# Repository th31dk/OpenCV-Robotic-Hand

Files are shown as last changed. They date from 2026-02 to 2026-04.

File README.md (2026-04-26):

<h1 align="center">
    EchoHand
</h1>
<h4 align="center">
    A robot hand that mirror's your every gesture
</h4>



<h2 align="center">
A Bit About This Project
</h2>
This project originally started as a ASL Interpreter. However, while researching ways to teach it signs, I discovered computer vision and how you can make robots copy you. Last year, I went to Prototype, a hackathon hosted by Hack Club. There, we had to train these SO-101 Robotic Arms to perform certain actions. The teleoperator part of the training stuck to me the most, so this project was born!

<h2 align="center">
Assembly
</h2>

### Hardware
#### [Bill Of Materials](/BOM)
|Part Number|Part Name |Quantity|Sourcing Link |Cost  |Notes|
|---|---|---|---|---|-----|
|1 |Arduino Uno |1 |https://www.aliexpress.us/item/3256808569187520.html|$5.65 | |
|2 |Breadboard |1 |https://www.aliexpress.us/item/3256806927240551.html|$1.92 | |
|3 |Dupont Wires |17 |https://a.co/d/0hN85zCM |$8.99 | |
|4 |External Power Supply|1 |https://a.co/d/045DWk0g |$59.99| |
|5 |DS3225 Servo |5 |https://a.co/d/0iK4KOZB |$90.00| |
|6 |M3x10mm BHCS |24 |https://www.aliexpress.us/item/2255800794906149.html|$1.86 | |
|7 |M3x10mm SHCS |2 |https://www.aliexpress.us/item/3256804341271555.html|$1.50 | |
|8 |USB-A to USB-B Cable |1 |https://a.co/d/0aNsTbvj |$7.21 | |
|9 |Webcam |1 |https://a.co/d/0bebSZXz |$25.00| |
|10 |Fishing Line |2000mm  |https://a.co/d/07G4QxGr |$9.98 | |
|11 |Elastic Cord |600mm |https://a.co/d/07XXOlZX |$9.99 | |

### [3D Printed Parts](/List%20Of%203D%20Printed%20Parts.csv)
3D files can be found [here](/Print%20Files/)

|Part Number|Part Name |Quantity|Material |Total Grams|Notes |
|---|---|---|---|---|---|
|1 |Finger 1 |5 |PLA |17.69 | |
| | | |PETG |0.34 |PETG for easy support removal|
|2 |Finger 2 |5 |PLA |20.15 | |
| | | |PETG |0.38 |PETG for easy support removal|
|3 |Finger 3 |4 |PLA |14.95 | |
| | | |PETG |0.37 |PETG for easy support removal|
|4 |Thumb |1 |PLA |7.33 | |
| | | |PETG |0.77 |PETG for easy support removal|
|5 |BackStand |1 |PLA |133.6 | |
|6 |Palm |1 |PLA |28.9 | |
|7 |Pin |11 |PLA |0.71 | |
|8 |Spool |10 |PLA |23.44 | |
|9 |Support |1 |PLA |44.39 | |

### Wiring Diagram
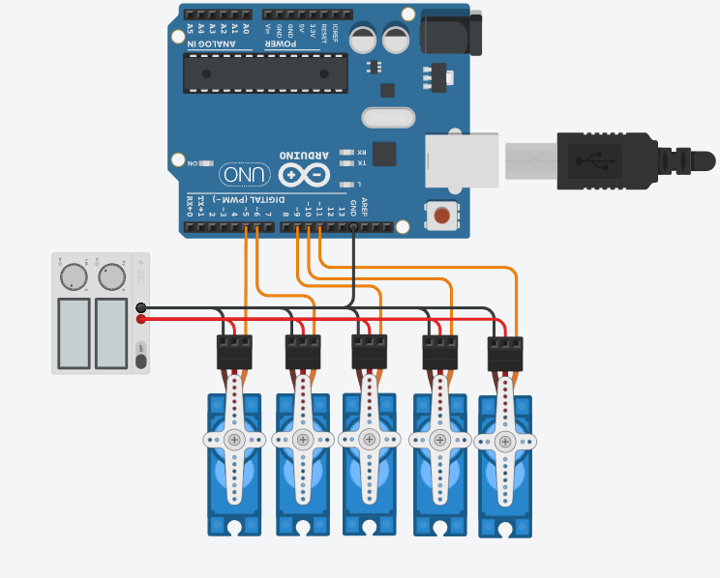
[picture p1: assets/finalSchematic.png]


### Starting the Program
Once you are done assembling the hand and connecting all the wires, you can just start up the python code and it'll start working automatically. Just hold out a hand and start making gestures! 

[Here's the Demo!](https://www.youtube.com/watch?v=Rfja3hf1nRA)

### Credits
Thank you to:  
Hack Club for supporting me throughout this project

Made by Horizon on Youtube for inspiring me to make this project. Check his [robotic hand](https://www.youtube.com/watch?v=aHFo-7ZK1Bk&t=697s) out!

MateoTechLab for making the amazing videos that encouraged me to make this and pursue hardware! Go watch his video [here](https://www.youtube.com/watch?v=NimROnJeQDY&t=253s)!

notaroomba for his amazing README layout! His [Trace](https://github.com/notaroomba/trace) project is super cool!

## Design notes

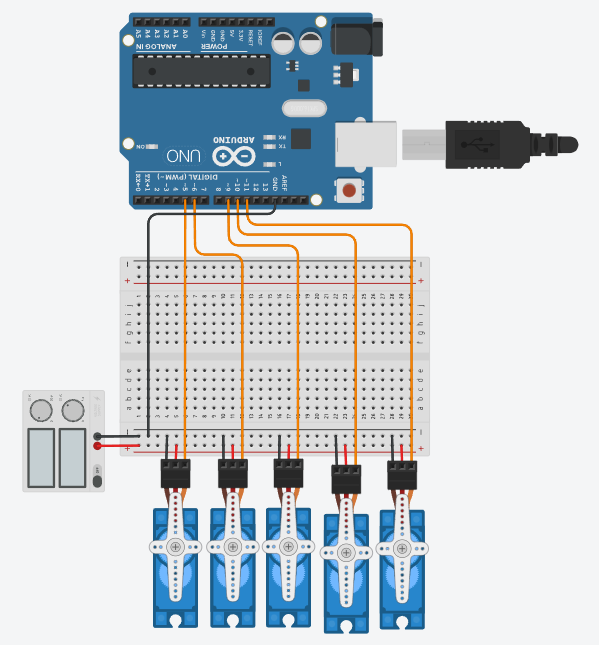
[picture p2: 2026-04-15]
assets/roboticHand_schematic_2.png

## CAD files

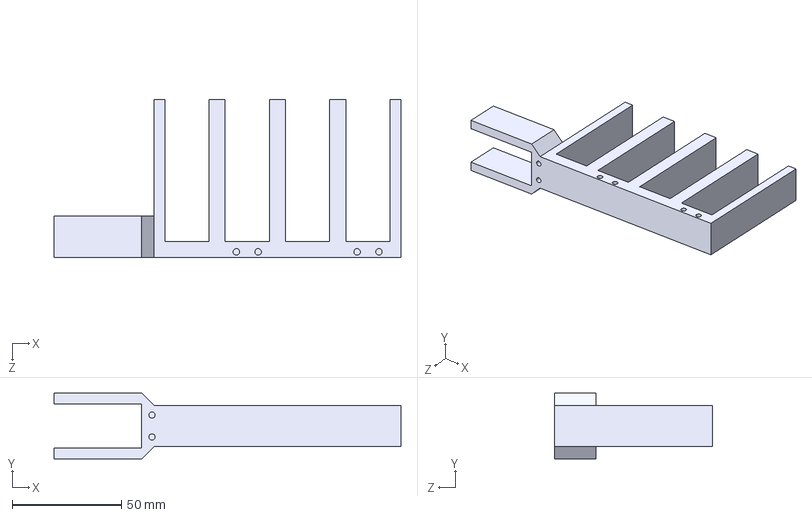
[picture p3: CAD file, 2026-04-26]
Print Files/servomount.STEP
159.1 x 30.2 x 72.2 mm

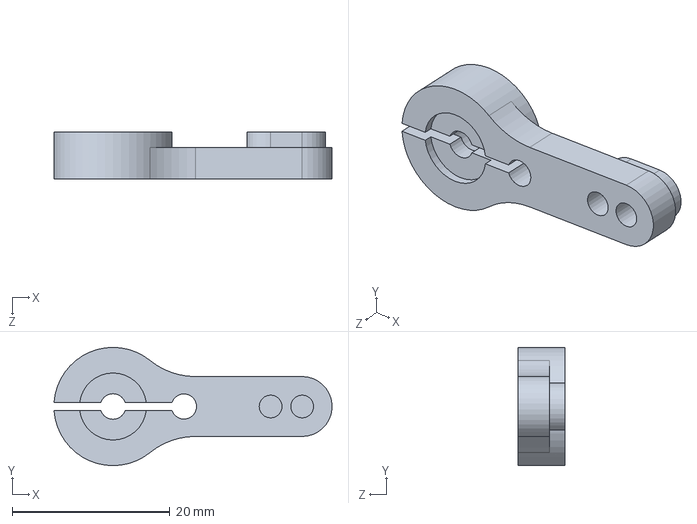
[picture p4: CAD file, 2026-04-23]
Source Files/servohorn.SLDPRT
35.3 x 15.0 x 6.00 mm

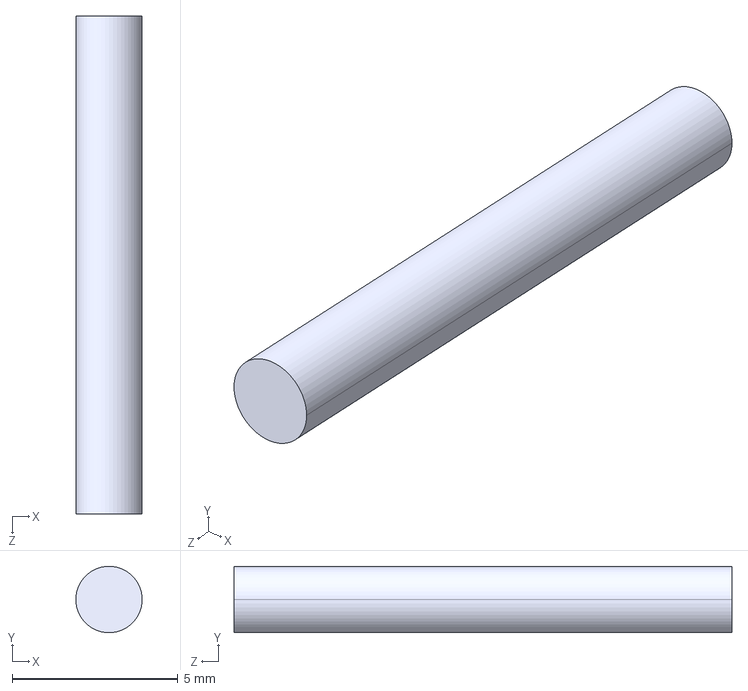
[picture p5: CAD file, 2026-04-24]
Print Files/pin.STEP
2.00 x 2.00 x 15.0 mm

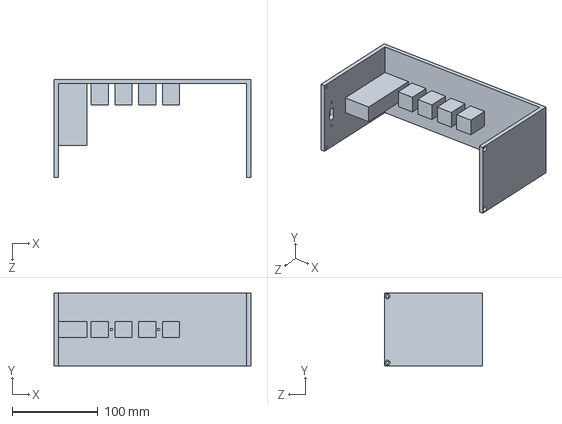
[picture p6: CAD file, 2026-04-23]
Source Files/forearmback.SLDPRT
230.0 x 85.0 x 115.0 mm

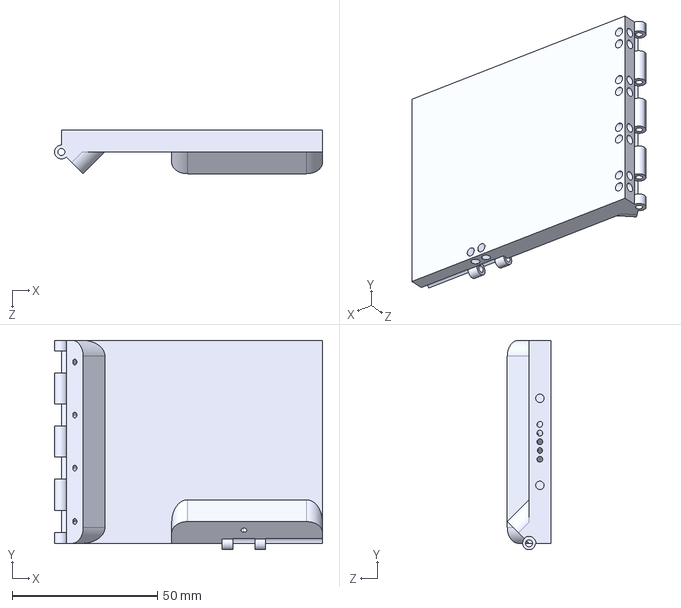
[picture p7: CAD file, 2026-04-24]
Print Files/Palm.STEP
92.4 x 72.2 x 15.0 mm

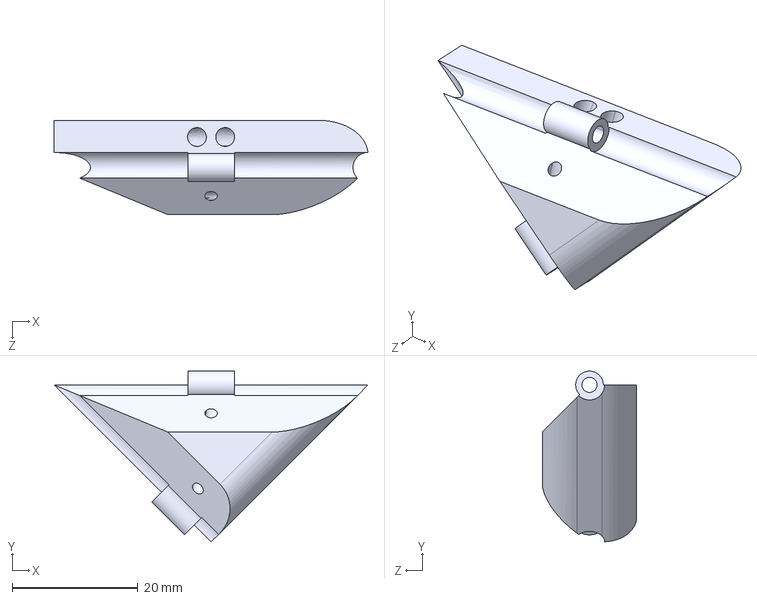
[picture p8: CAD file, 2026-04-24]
Print Files/Thumb.STEP
50.0 x 27.2 x 15.0 mm

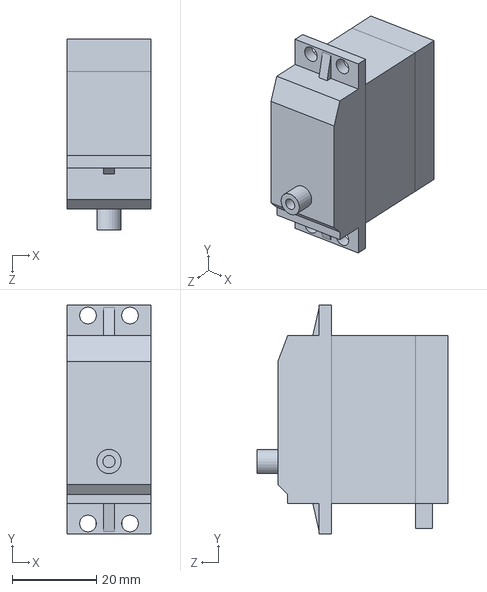
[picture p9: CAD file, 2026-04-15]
Source Files/DS3225MG.SLDPRT
20.0 x 54.5 x 45.5 mm

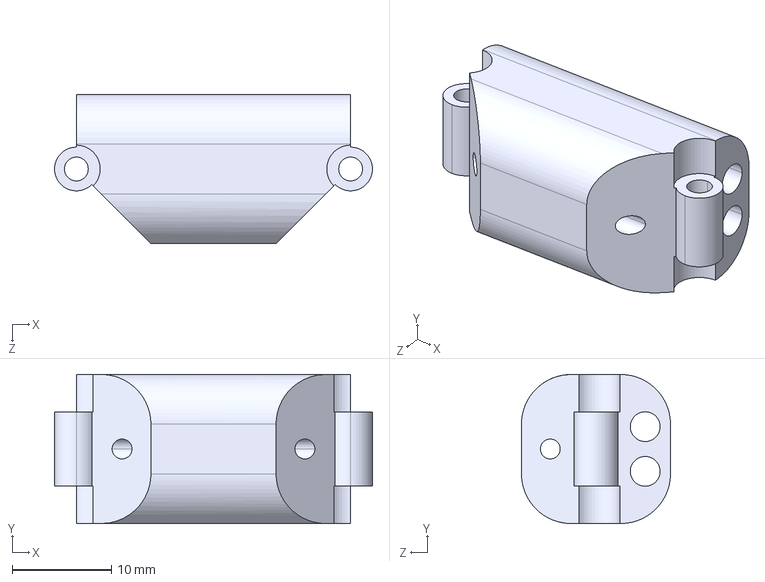
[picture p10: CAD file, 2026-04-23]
Print Files/Finger3.STEP
32.0 x 15.0 x 15.0 mm

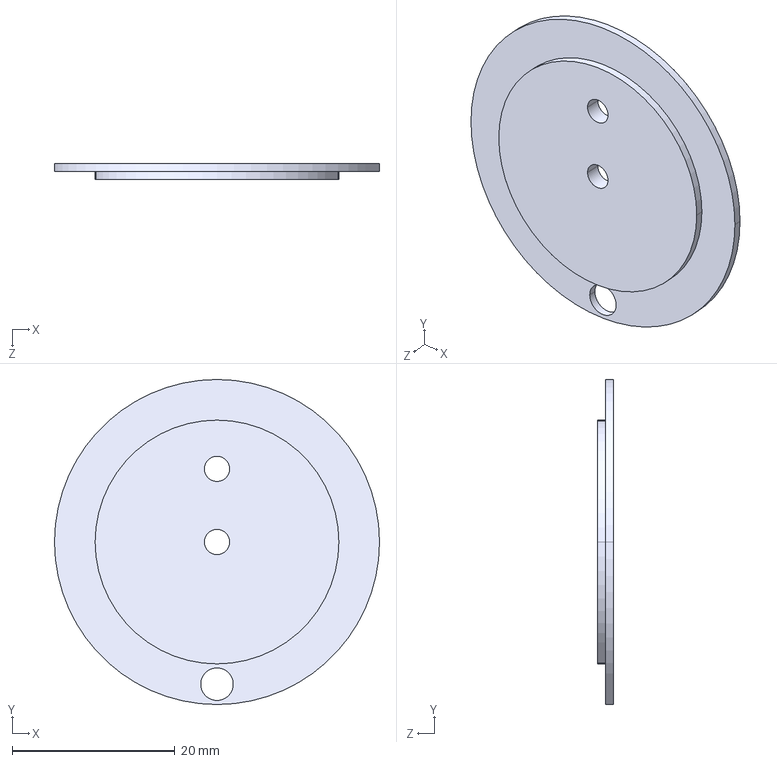
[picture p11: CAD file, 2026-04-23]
Print Files/spool.STEP
40.0 x 40.0 x 2.00 mm

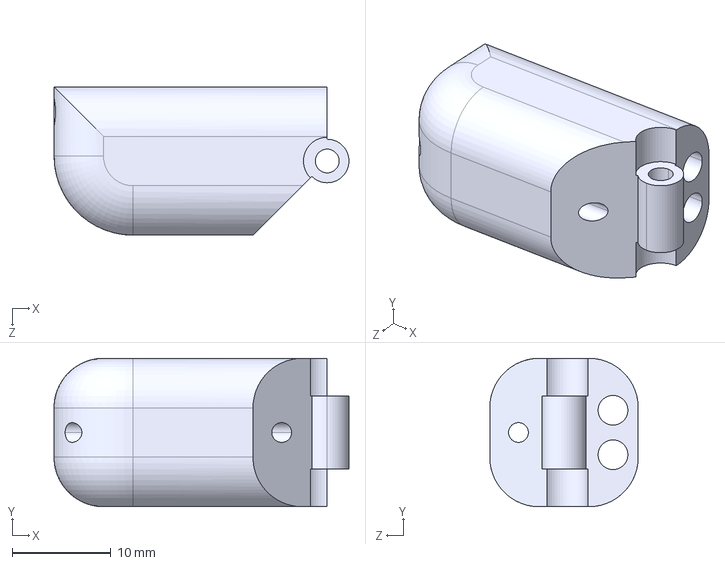
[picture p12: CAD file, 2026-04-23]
Print Files/Finger1.STEP
29.8 x 15.0 x 15.0 mm

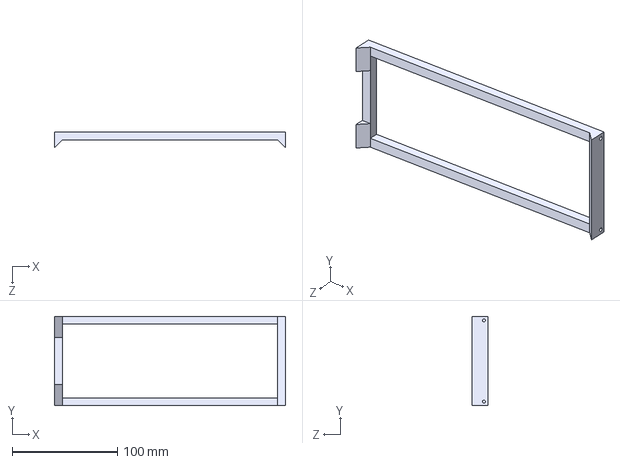
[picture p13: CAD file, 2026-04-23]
Print Files/Support.STEP
220.0 x 85.0 x 15.0 mm

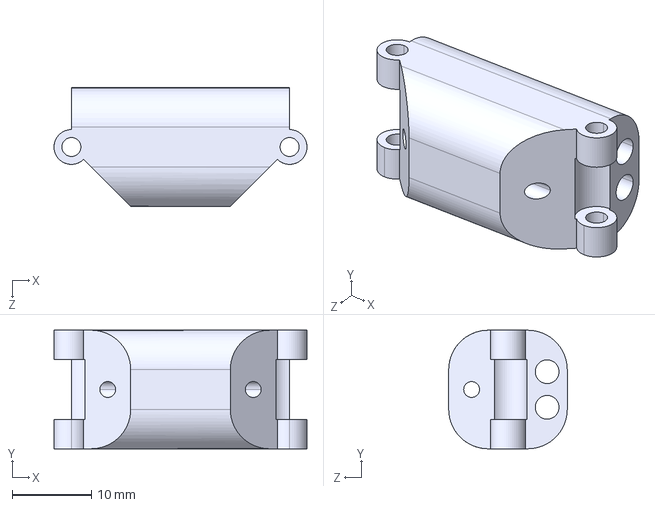
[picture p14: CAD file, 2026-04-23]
Print Files/Finger2.STEP
32.0 x 15.0 x 15.0 mm

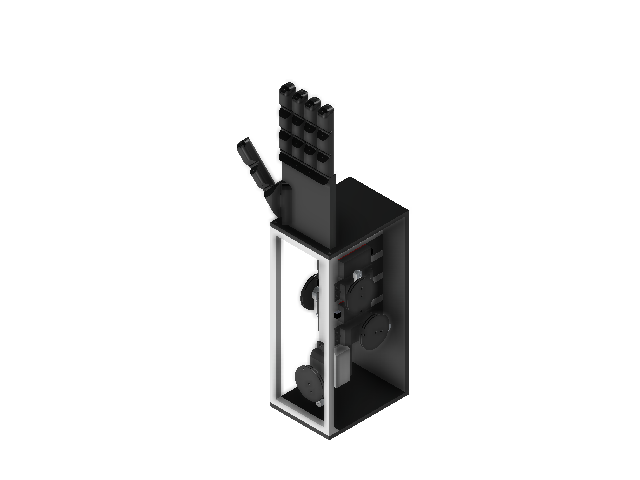
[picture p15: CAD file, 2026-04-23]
Source Files/Assembly.SLDASM
DS3225MG x 5
servomount
Support
Hand
Finger1 x 5
Finger2 x 5
Finger3 x 4
Thumb
servohorn x 5
spool x 10

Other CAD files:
Print Files/BackStand.STEP
Source Files/Finger1.SLDPRT
Source Files/Finger2.SLDPRT
Source Files/Finger3.SLDPRT
Source Files/Palm.SLDPRT
Source Files/Support.SLDPRT
Source Files/Thumb.SLDPRT
Source Files/pin.SLDPRT
Source Files/servomount.SLDPRT
Source Files/spool.SLDPRT

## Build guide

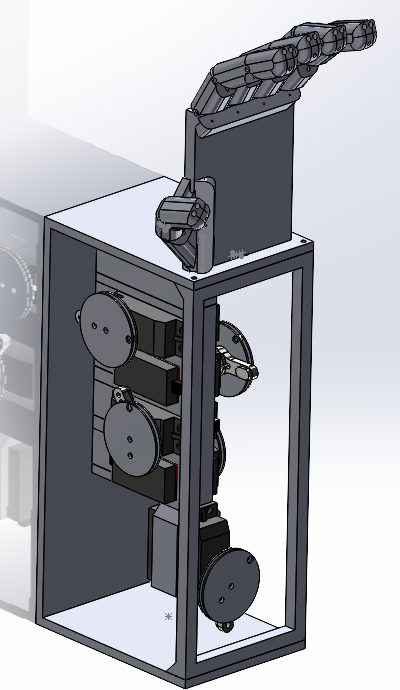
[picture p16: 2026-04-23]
assets/assembly.png

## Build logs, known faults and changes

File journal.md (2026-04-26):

# Notebook Information
Hey guys, this document will be where I track my progress on this project.  
## Engineering Design Process
Throughout this project, I will be using the engineering design process to iterate on my designs:

Identify the problem  
Brainstorm Solutions  
Implement The Best One  
Build The Model  
Test For Problems  

# Notebook Entries
## February 6th, 2026 - Friday - ~3 hours of progress
Today, I designed the first prototype of the index finger. This design will be the base of each finger besides the thumb.  

### Design
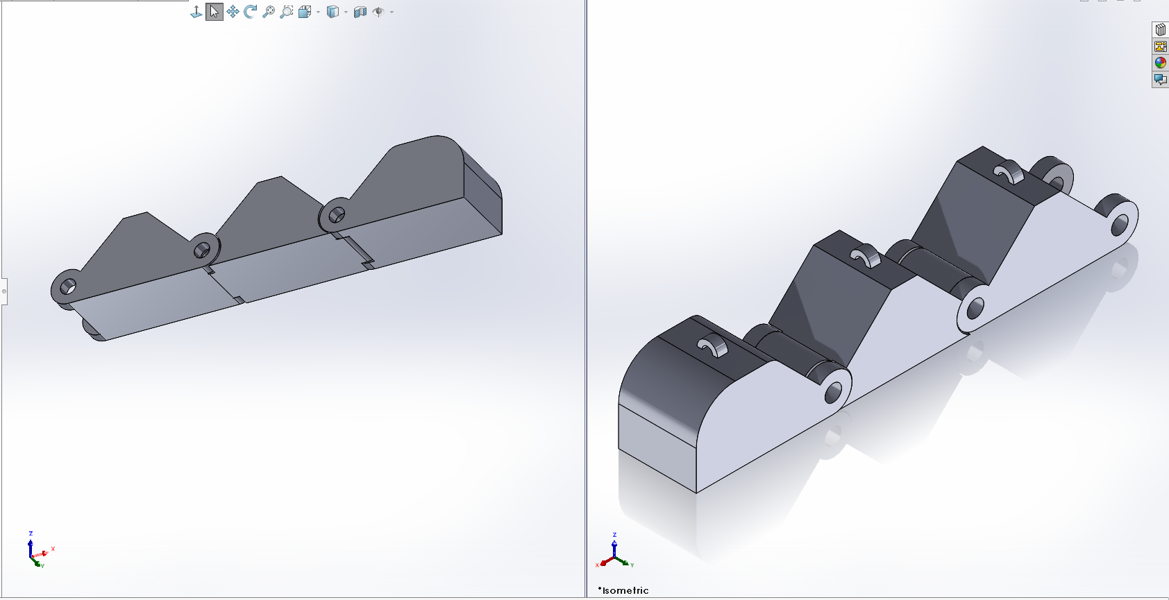
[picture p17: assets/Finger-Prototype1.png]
  

Since fingers mainly move in one axis I decided to use a resolute/hinge joint for each segment of the finger. For the pins of each hinge, I took inspiration from my school's VEX V5 team. We often use screws to act as pins for hinges, so I decided to use that in my design. I designed each hole to have a diameter of 3.2mm to account for the tolerance of my 3D printer and used M3 screws.  

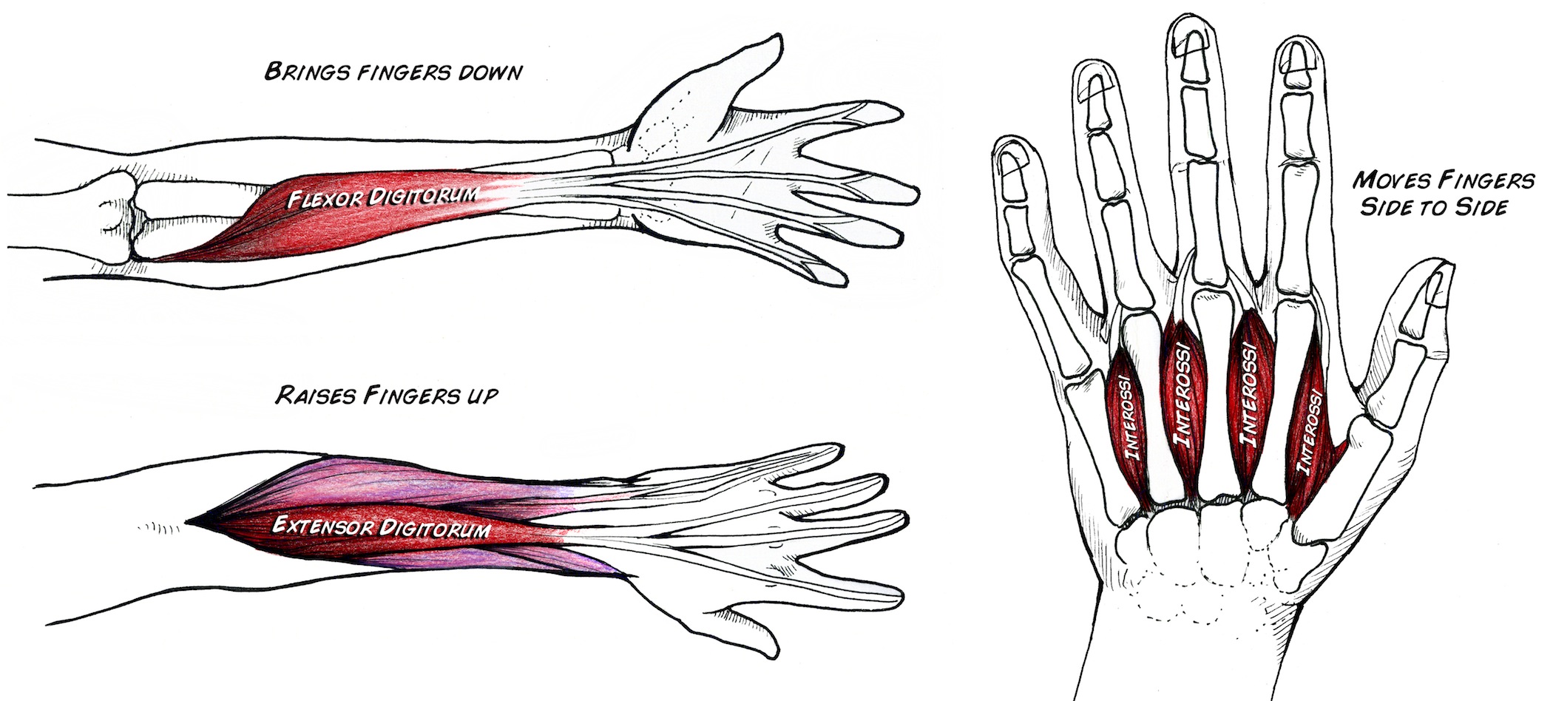
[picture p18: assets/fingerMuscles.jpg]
  
Above, you can see a chart that shows the different muscles controlling your fingers. Something unique about the fingers is that there are no actual muscles located inside them. Instead, your body uses muscles in your forearm to move your fingers. These muscles pull on tendons which control how much your fingers are bent. To replicate this, I bought fishing line to act as the tendons and used servos I already had to act as the muscles.

### Build
I sliced the 3D model in Bambu Slicer and used lightning infill because the printed model is just a prototype. I used black PLA for this, and it took approximately 20 minutes.  
After I was done printing it, I aligned all the segments together and put in a M3x20mm screw to act as the pin for the hinges. The screw didn't fit in that well so I drilled the hole with a 3mm drill bit. Tying the fishing line was definitely the hardest part because it didn't want to tie no matter what.

### Testing and Identifying Problems
#### Problem 1
I quickly realized that the finger had no way to lift back up after being pulled down.

#### Problem 2
I also noticed that the finger could bend backwards. This was not only unnatural but made it so I couldn't pull it back down.

## February 7th, 2026 - Saturday
Hey guys! Today, I worked on the second prototype of the finger, addressing some of the major problems I found with the first prototype.
### Design
#### Solution to Problem 1
1. **Use another servo and more fishing line**
    I could use another servo to act like another muscle.
2. **Use elastic cord**
    This solutions is cheaper and easier to implement, so I will choose this. 
#### Solution to Problem 2
Instead of positioning the pin at the very bottom of each joint, I can put it half way. This way, the flat part below the pin will stop the finger from being bent back. 

### Build
Once again, I sliced it in Bambu studio and kept all the settings the same. However, since theres now a holder for the elastic cord, I had to print it sideways with support. I used PETG for support interface to make sure the support is easy to remove. 
After I was done printing it, I assembled it again. 

### Testing and Identifying Problems
The new design worked good and I was ready to move on to the servos.
#### Problem 1
The servos I tested, SG90 and HS-422 were not powerful enough to overcome the elastic cord.

#### Problem 2
Each bolt sticks out a little, making it hard to make the hand compact. 

### Brainstorming Solutions
#### Solution to Problem 1
I will be purchasing stronger servos on Amazon, specifically DS3225 servos.
#### Solution to Problem 2
I found these small metal pins on Amazon that should fit the fingers perfectly.
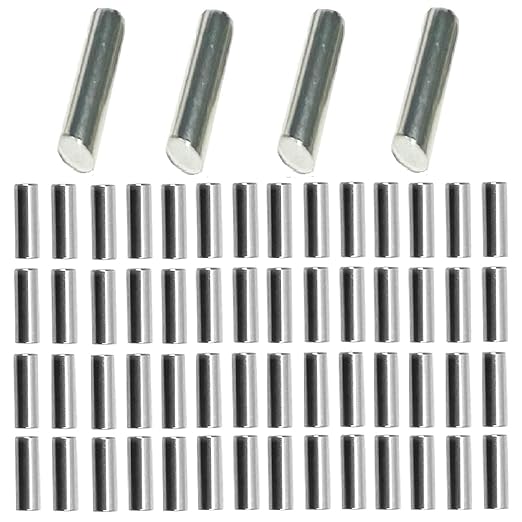
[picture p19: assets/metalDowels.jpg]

I might also consider printing plastic rods instead to save cost. 
## February 8th, 2026 - Sunday
Today, I received the new servos and tested them. The servos ended up working fine and were perfect for the job.

## February 9th, 2026 - March 12th, 2026
I worked on filling out the notebook. I also took a break from this project at this time.

## March 13th, 2026 - Friday - ~1 hour of progress
### Design
Today, I modeled the DS3225 servo so I could have an easy reference when modeling the palm for the hand. 
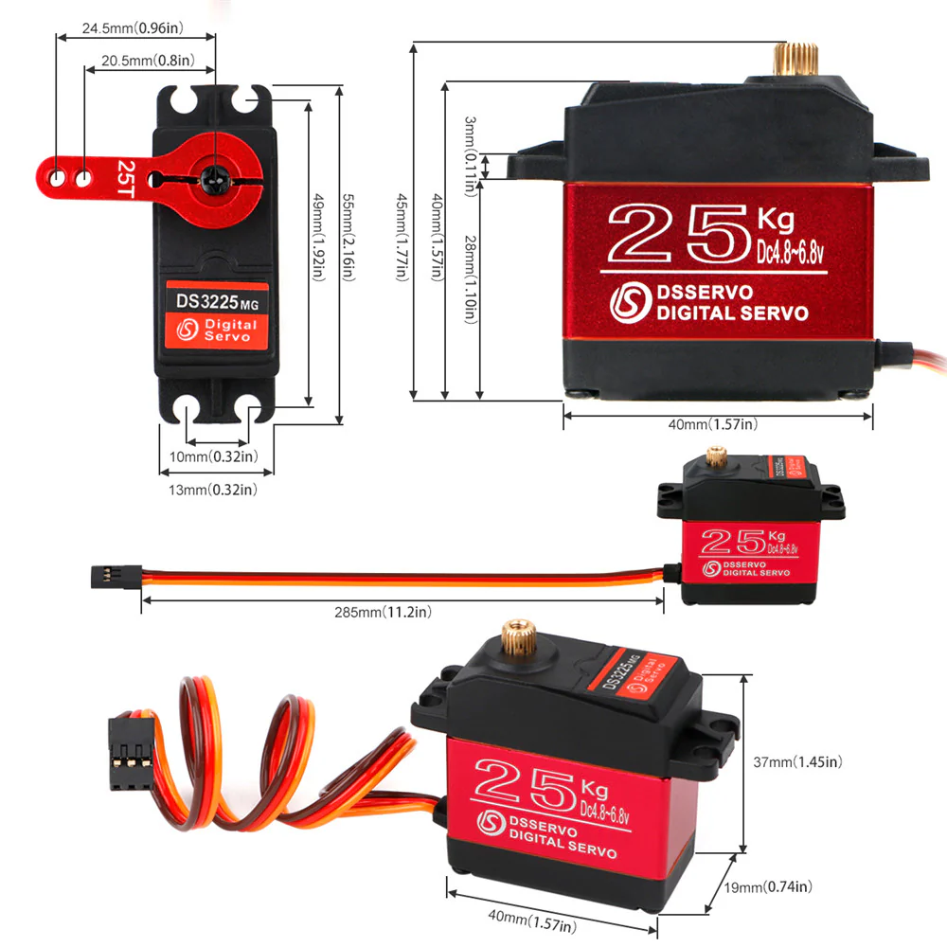
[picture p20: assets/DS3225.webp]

## March 14th, 2026 - Saturday - ~1 hour of progress
### Identifying Problems
When testing the fingers that I modeled, I noticed that I had to pull on the string a lot for the fingers to fully close. There was no way that the motors could close that far.

### Solution
Since the circumference of a circle is always larger than  it's diameter, I decided to model a tiny spool, which would help with increasing the length of string it could pull. 

## March 15th, 2026 - Sunday - ~3.5 hours
### Design
Today, I decided to start working on the palm of the hand. One of the goals I had for the hand was to make it look natural, so I wanted it to be compact. Unfortunately, the design I came up with today was really chunky, but I will improve on the design in the future.

I only modeled part of the hand because I was only going to print a small portion of it to test if it would fit.
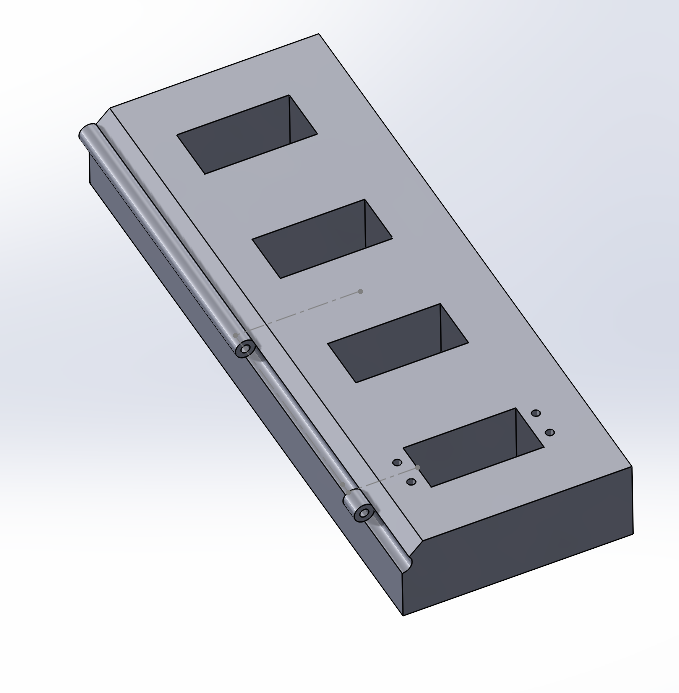
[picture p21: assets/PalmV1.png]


### Build and Testing
I printed the small portion in PLA.
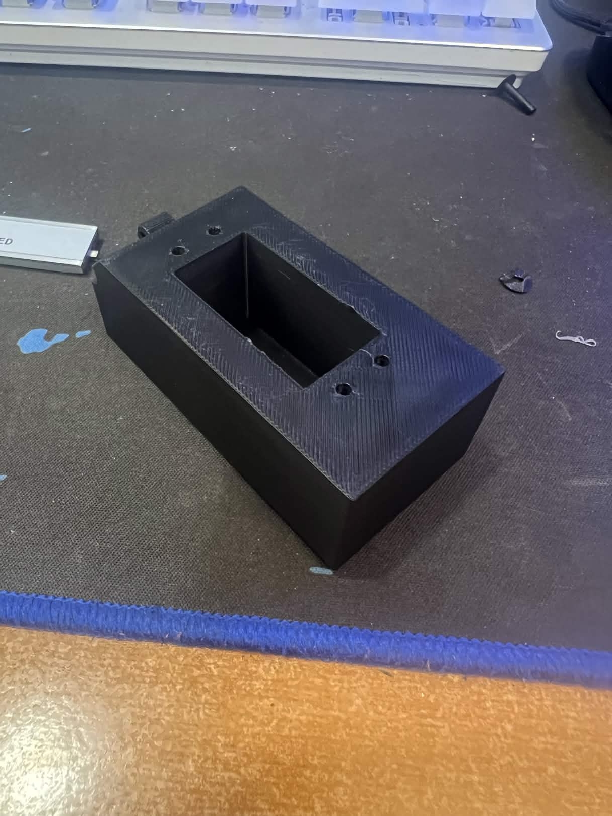
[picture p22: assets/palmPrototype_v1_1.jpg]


#### Problem 1
I didn't account for the wires on the servo, so the servo can't fit into the palm.

#### Problem 2
Since the servo is so close to the finger, the finger can't close all the way without hitting the servo.

#### Problem 3
This design uses a LOT of filament. The slicer estimated around 132g of PLA for the whole palm. If I kept this design, I would quickly waste all of my filament. 

### Design
I completely overhauled the design. I made the base thinner so that the wire could pass through the palm completely. This thinner design helped reduce the cost of filament as well. The cost went down from 42g to 12g for a single finger. I also moved the servo back so that the finger would never contact the servo when its being pulled down.

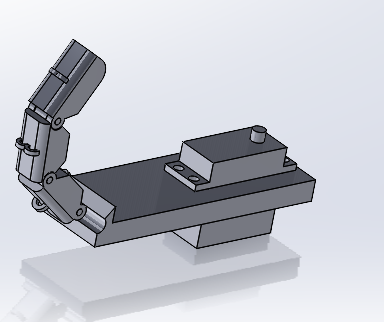
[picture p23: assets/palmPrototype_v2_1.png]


### Build and Testing
Once again, I printed this out of PLA. 

#### Problem 1
This new design didn't fix problem 1 because I couldn't get the stub through the hole because the hole was designed for the servo without the stub.

#### Problem 2
Although the finger doesn't touch the servo anymore, it can't fully close because it is blocked by the palm.

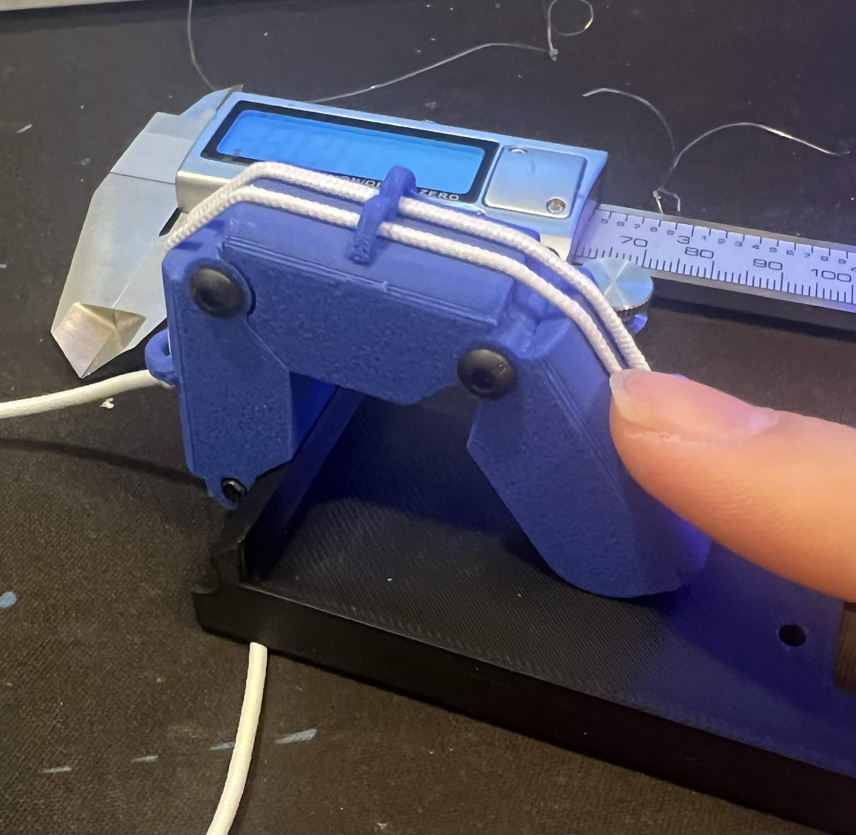
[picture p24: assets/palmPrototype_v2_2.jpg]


### Design
Third times the charm! I hope... 
#### Solution 1
I cut a hole into the palm so that the stub could pass through cleanly.
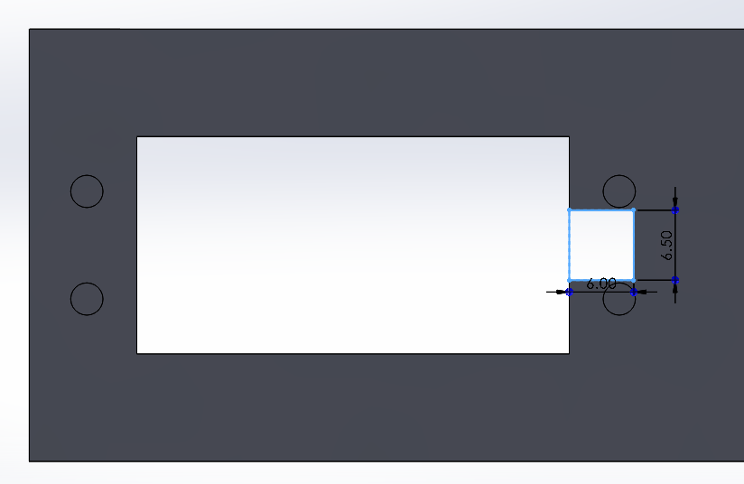
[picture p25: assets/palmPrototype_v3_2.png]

#### Solution 2
I moved the hole for the pin even higher up so that the finger tip wouldn't hit the palm anymore. 
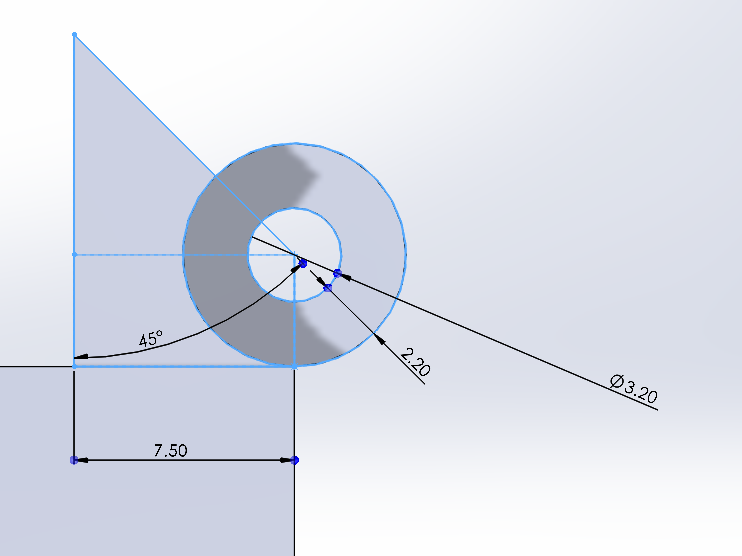
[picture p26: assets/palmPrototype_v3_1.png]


### Build and Testing
Not so surprisingly, I printed this out of PLA. This design solved all the problems that I noticed in my old iterations, but other problems showed up quickly. 

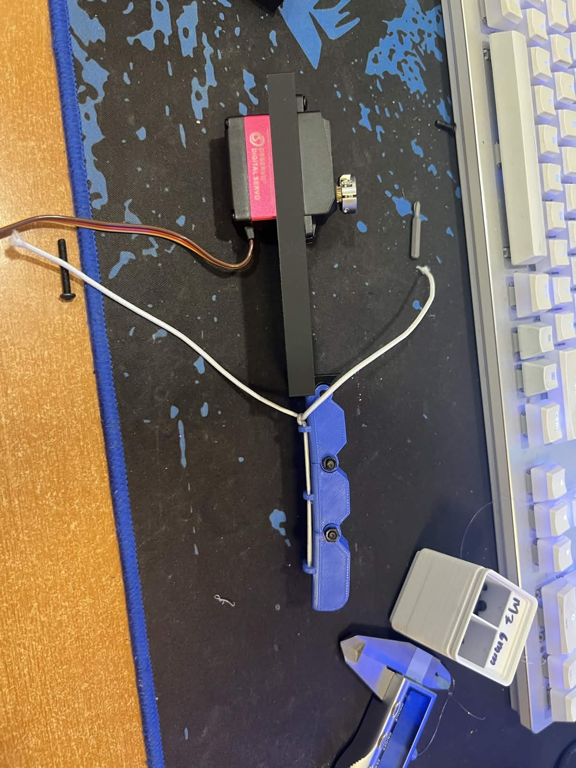
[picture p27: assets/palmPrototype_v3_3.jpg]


#### Problem 1
There's no way for the elastic cord to attach to the palm, so it has no way to return to the normal position. Instead, it stays at a 90 degree angle with the palm when not activated. 

#### Problem 2
Theres no way to route the fishing line, so when the finger is pulling, it gets blocked by the fishing line. 

## March 16th, 2026 - Monday - ~0.5 hours of progress
### Design
Today, I couldn't spend much time on this project because of school. However, I modeled a better design of the palm. For this new iteration, I want to implement a forearm which will hold all my servos instead of storing the servos in the palm. I haven't modeled the forearm with the servo holders yet, but here's what I modeled!

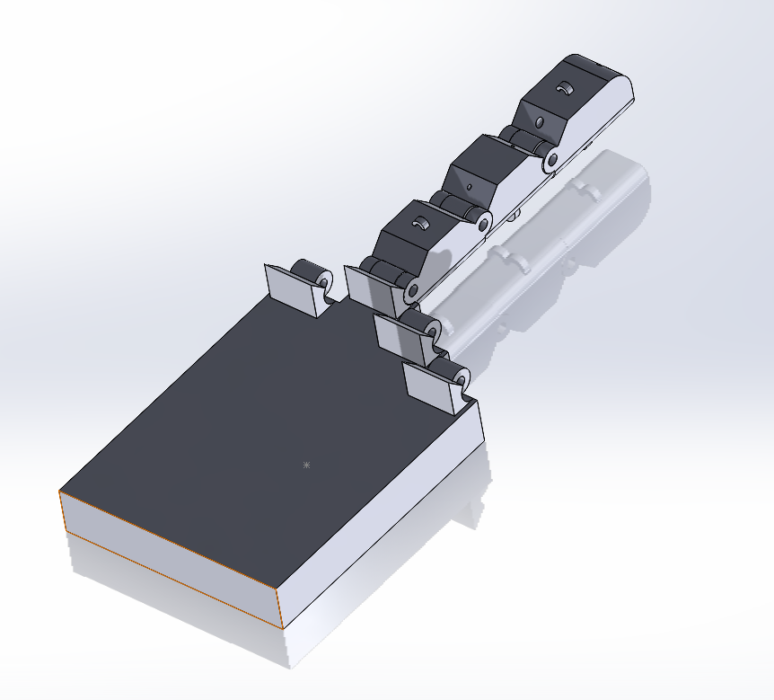
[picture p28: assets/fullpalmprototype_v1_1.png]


I still need to figure out how to model the thumbs but it's getting late. Good night!

## March 17th, 2026 - Tuesday
Today, I wanted to start coding so I could test my servos. I think that coding will take the longest so I want to start now.
To control the finger, I want to use an Arduino R3 I have.
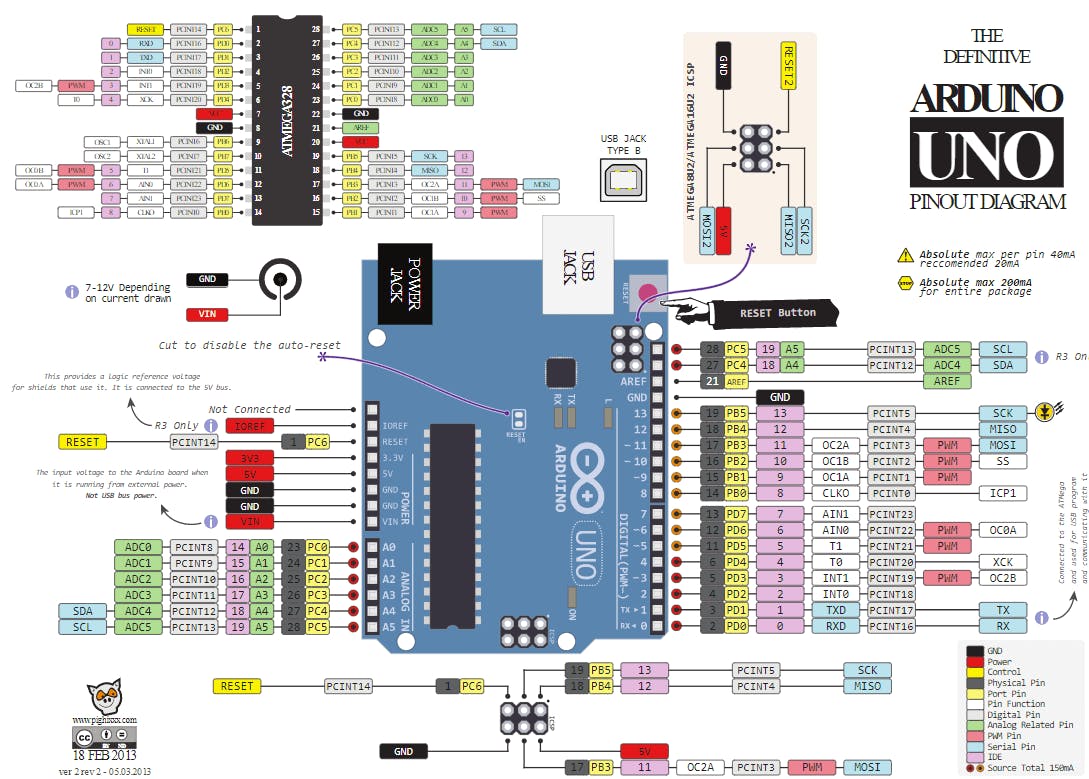
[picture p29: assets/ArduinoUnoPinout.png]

The servos are controlled with PWM, so I can only use pins 5, 11, 12, 15, 16, 17. This should be enough pins because I only have 5 fingers. In the future, I might upgrade to an esp32 for more PWM pins if needed.

This is one of my first times programming in C++ so this might take a while.

### Identify the Problem
I need a way to find how much my servo needs to pull for the hand to fully close.

### Brainstorm Solutions
I can write a program where I can tell the servo to go to a certain angle. When I find the write angle, I can write it down.

### Implement the Best Solution
I've started coding the servos on Arduino IDE. 

### Identify the Problem
The overall goal of this hand is to be able to see my fingers and it's position and mimic that onto the hand. 

### Brainstorm Solutions
When researching ways for the computer to see and process my hand, I stumbled across OpenCV. OpenCV is a library thats made for computer vision. Using computer vision, I can see what angle each segment of my fingers are at. 

I've read through this article by OpenCV and it seemed to match what I wanted.
https://opencv.org/wp-content/uploads/2020/11/Universal-Hand-Control.pdf

## March 19th, 2026 - Thursday - ~0.5 Hour
Today, I drew out the schematic of the robotic arm. It's pretty simple but it doesn't need to be very complicated. 
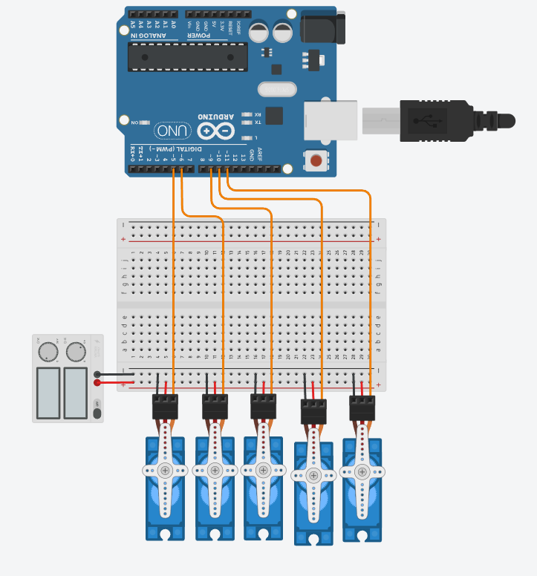
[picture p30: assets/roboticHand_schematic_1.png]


I'll be using a DC Power Supply to power the servos. The Arduino will be powered by my PC through the USB port. I'm a bit worried that the servos will draw too much current. However, my power supply has overcurrent protection so it shouldn't burn my house down.  

On Tuesday, I'm not sure why I thought 12, 15, and 16 had PWM function. I looked closer at the board today and realized that the pins with the tilde were the only ones with PWM features.  

Thats all I did today! See you tomorrow!

## March 21st, 2026 - Saturday
Happy Saturday! I'm so glad that it's the weekend. Today, I want to work on the design of the hand and address a problem that I have with my current finger design.

### Design
#### Identifying Problems
The problem that I have with the current design is that the current aligners for the elastic cord stick out the top of the finger. The current design doesn't look good and is hard to 3D print.

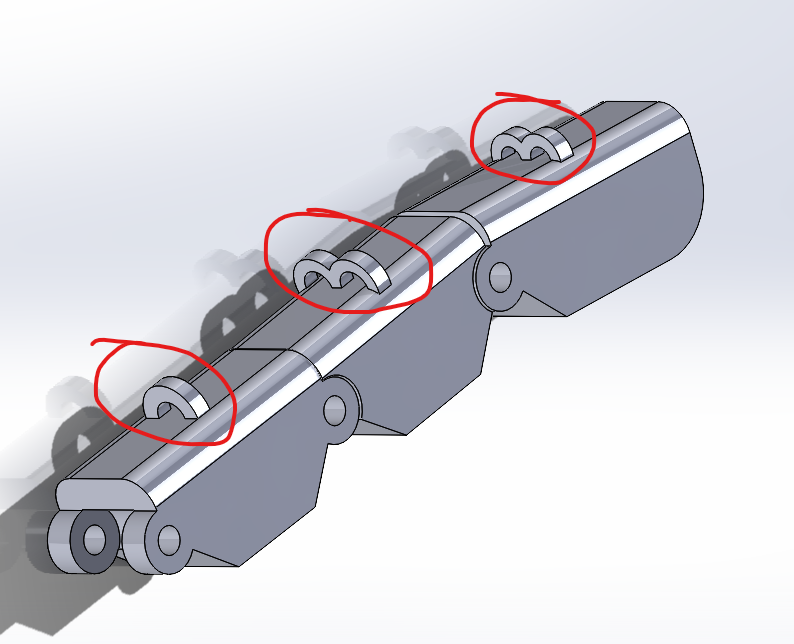
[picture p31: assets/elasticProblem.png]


#### Solution
I plan to fix this by cutting holes into the finger. This will likely need completely new design because the slots of the holes take up too much space. I might switch to 1 or 2mm pins instead of 3mm pins to save space.

Now that we have identified our solution, lets start designing!

Here's my updated design!

|New|Old|
|---|---|
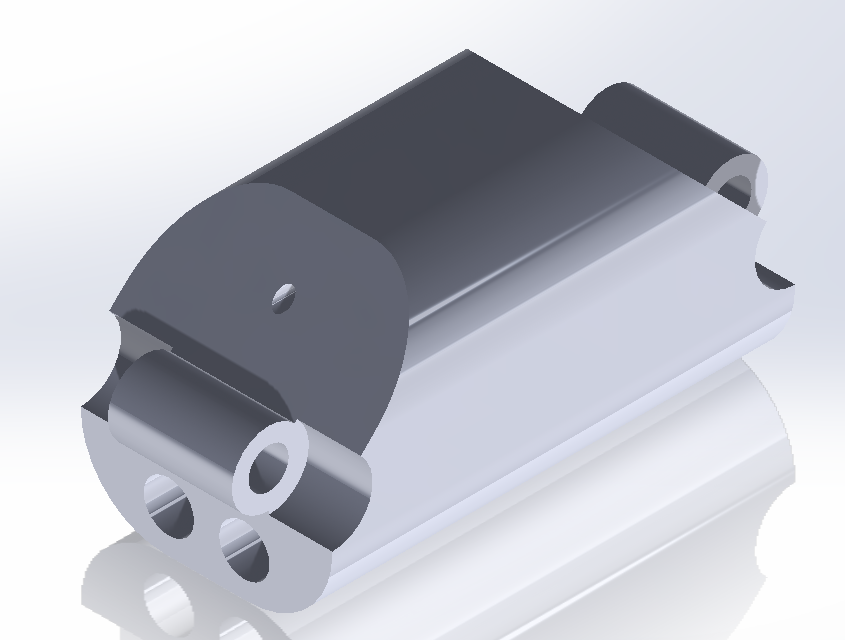
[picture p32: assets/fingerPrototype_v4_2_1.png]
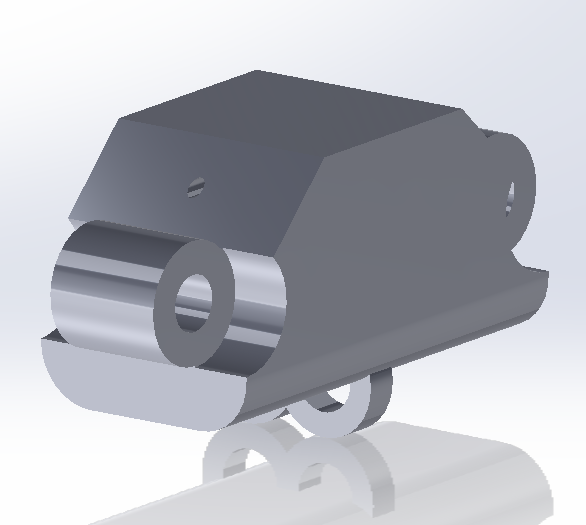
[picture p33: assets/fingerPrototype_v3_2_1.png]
|||

As you can see, I've moved the holes to inside the finger and used a smaller pin hole. This has allowed me to increase the filet on the finger. making it look better.

I've printed the segment in PLA on my Bambu P1S. I also printed one in TPU because I want to test if it will give me extra grip when holding items.

I think the new design works fine. I still need to model the other finger segments, so I won't know if the design is perfect until then. I'll start working on the next segments now. 

TADA!
|Segment 1|Segment 2|Segment 3|Full Assembly|
|---|---|---|---|
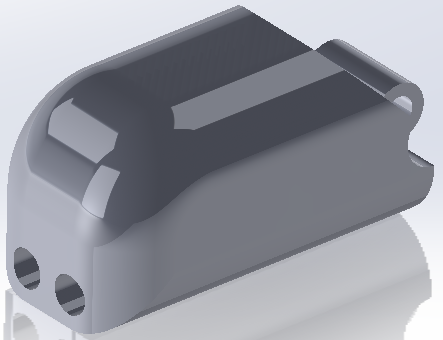
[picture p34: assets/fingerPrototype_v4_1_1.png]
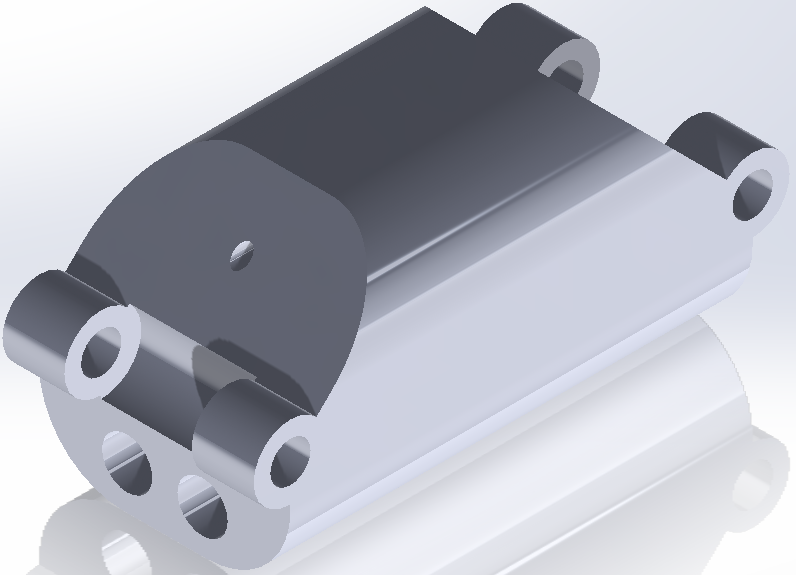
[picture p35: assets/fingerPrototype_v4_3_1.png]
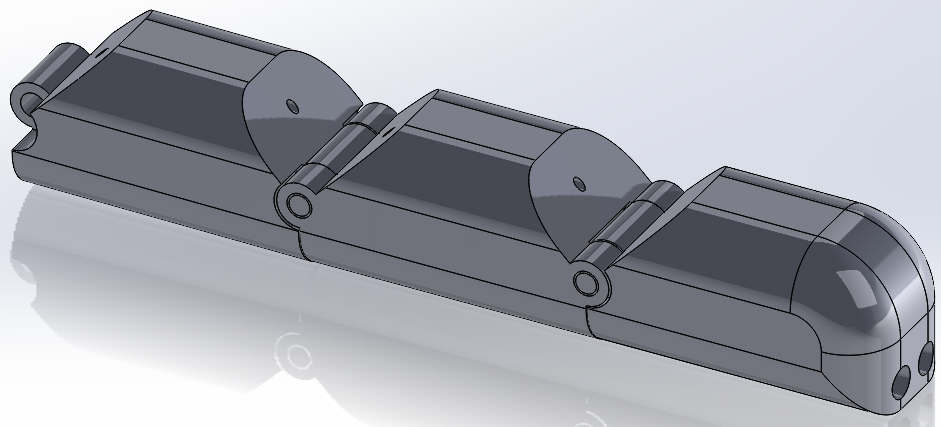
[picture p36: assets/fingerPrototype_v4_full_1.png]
|||||

Since I didn't have any m2 bolts and nuts, I just modeled a 2mm cylinder to act as a pin. Hopefully this will reduce the overall cost of the hand.

#### Testing and Identifying Problems
I printed all the segments and the pin out of Black PLA. It didn't really work after putting it together because the circles were misshaped. 

#### Solution
I think this is because I printed it in a different orientation that I usually print it. I tried this different orientation because I didn't want to use support, but I will print again and see.

#### Testing and Identifying Problems
It worked! You should definitely print circles and arcs parallel to the print bed for better accuracy. 

Here's the assembled finger!
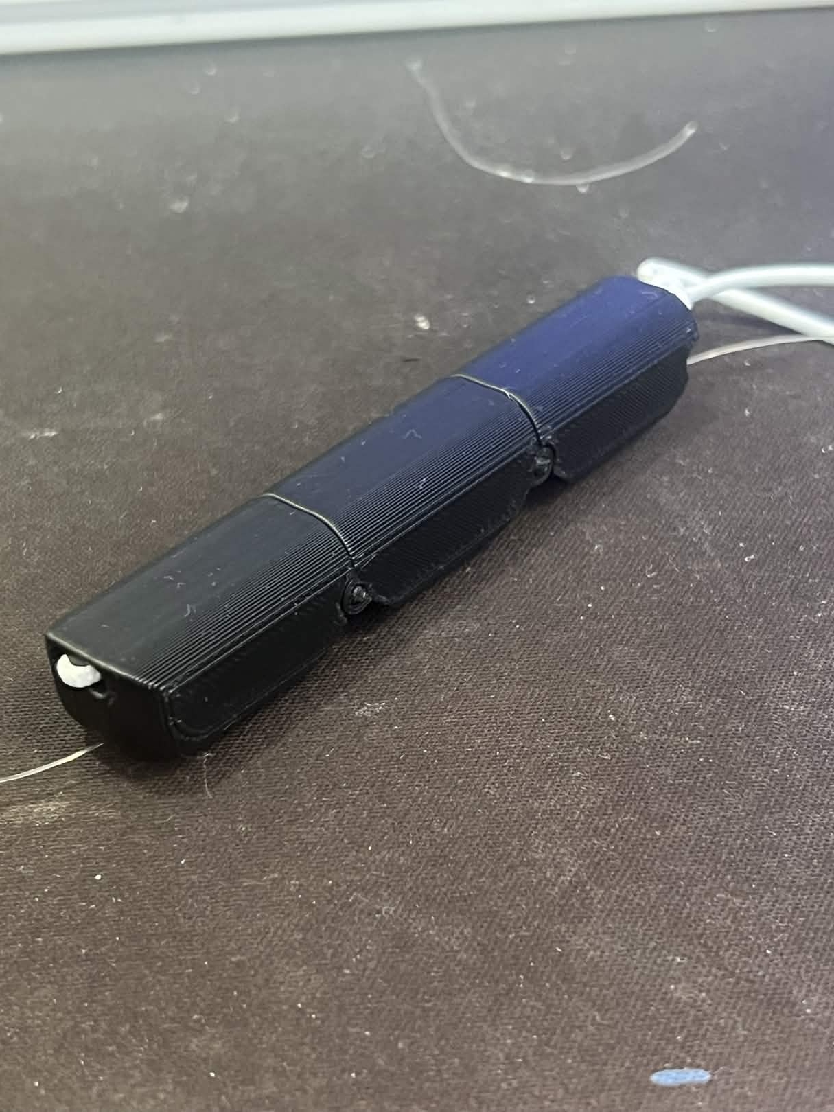
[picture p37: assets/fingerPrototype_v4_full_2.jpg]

It looks so clean compared to the old one.

## March 22nd, 2026 - Sunday
Today I want to continue modeling the hand and maybe code for a little bit. Let's get started!
### Design
Last week, I identified a few problems with the hand. One of which was that the string could not be routed so the finger ends up just hitting the string. I think I will completely redesign the hand because I now use 2mm holes instead of 3mm.

Drum Roll Please!

poof

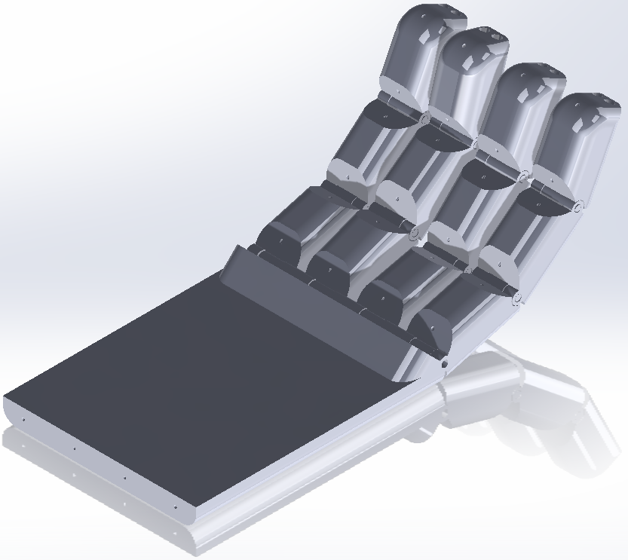
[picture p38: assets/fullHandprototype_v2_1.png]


The hardest part was definitely making the holes for routing the fishing line. It took me a while for me to line the two holes up perfectly. 

I still need to make a way for the elastic cord to be routed and the thumb.

I'm not sure how I'll model the thumb because it behaves so much differently from the other fingers. Like the other fingers, it has 3 segments, but one segment is build into your palm, so I likely need to cut a hole in the palm to mount it. 

It's kinda crazy how important your thumb is to holding things. I don't thing you can grip things well without your thumbs. Like try gripping picking stuff up without your thumbs. You'll quickly miss using your thumbs.

I decided not to print out the palm yet because it takes around 50g of filament to print. I'm trying to save costs as much as possible so I'm holding off until I model the thumb. 

I think that's it for today! I'll probably code a little bit over the week and continue the design over the next weekend. I also have spring break next week so I hope to finish the design and get a lot of the code done then. 

## March 29th, 2026 - Sunday
Hi guys! Today, I'll design the thumb of the hand. Like I mentioned earlier, this will likely be the hardest part of the hand to model, simply because of the different mechanism.

### Design
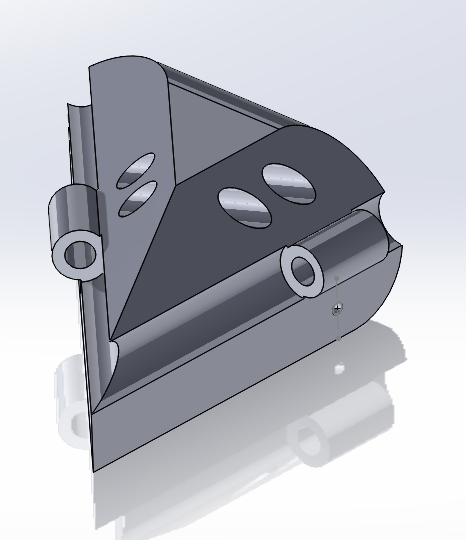
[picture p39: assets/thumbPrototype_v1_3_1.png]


Here's my first prototype! modeled the first segment at an angle because your thumb's first section is shaped like a triangle. kinda...

I had a big of trouble modeling the holes because they didn't enter or exit on the same axis. However, I learned about the sweep cut tool in SolidWorks. It basically stitches your two holes on different faces together.

Thinking I had a good design, I decided to build the full thumb in assembly. I decided to use segments from the other fingers. 
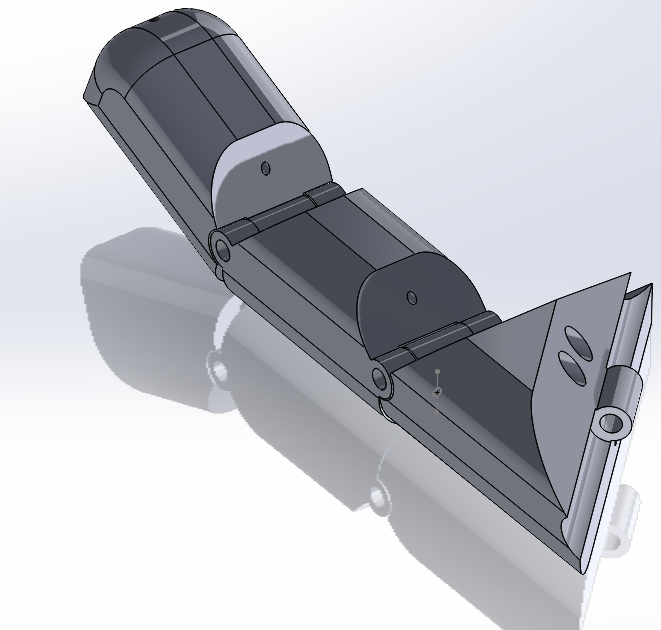
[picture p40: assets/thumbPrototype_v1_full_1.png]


## March 30th, 2026 - Monday
Today, I started by finishing up the palm design.

### Design
Again, I used the sweep tool in SolidWorks to converge the fishing line from the fingers down to the wrist area. 
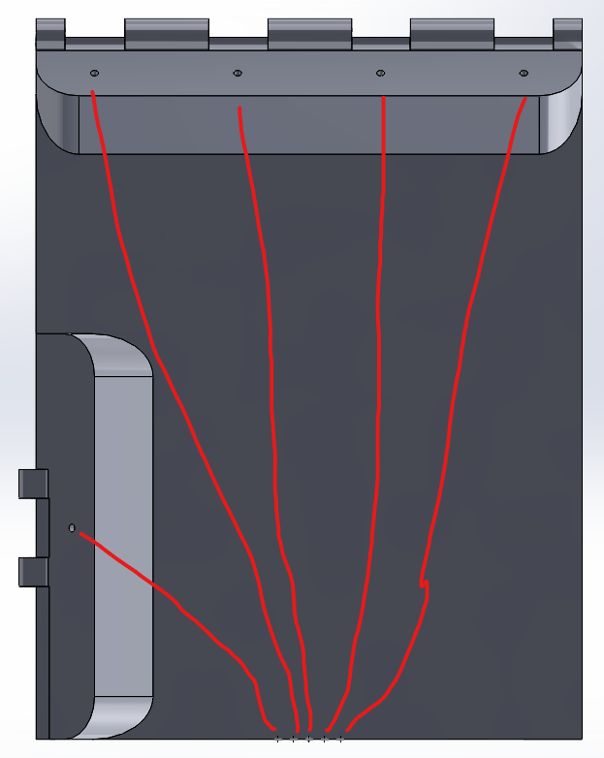
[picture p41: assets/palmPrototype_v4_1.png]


I also added the holes I need for the elastic cords to connect the the palm.
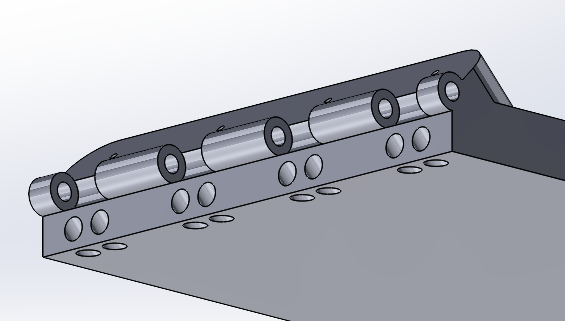
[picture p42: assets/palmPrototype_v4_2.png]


After that, I finished the assembly of the palm.
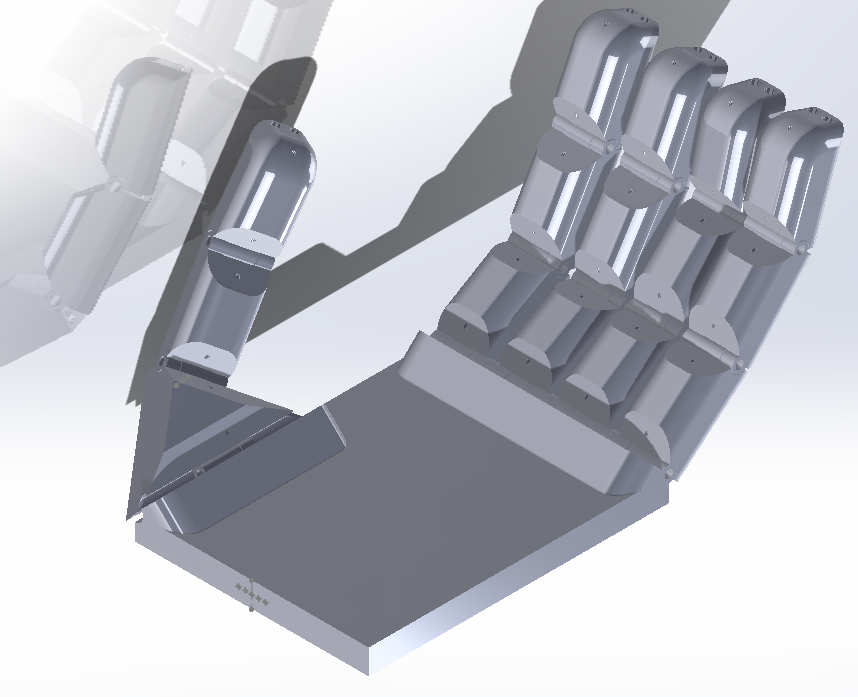
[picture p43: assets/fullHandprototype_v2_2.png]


To connect the 4 other fingers to the palm, I'm planning on printing a long rod so it'll be easy to pin 4 of them instead of having an individual pin for each finger. 

I'm pretty happy with this design. I'll have to print it all out and test it next.

## April 1st, 2026 - Wednesday
Happy April Fool's Day!

Today, I wanted to work on assembling and coding the hand. 

### Code
Through my research, I figured out how to have the microcontroller read my inputs to the serial monitor. I ran into some problems setting it up, but I think it's just a syntax problem.

I've referenced the example code in the Arduino docs and wrote code off of that to test out the serial monitor. The code is supposed to return the value that I put in, but it doesn't do that. Instead it returns a random string of numbers when I do. For example, when I input "1", it spits out "49 10"
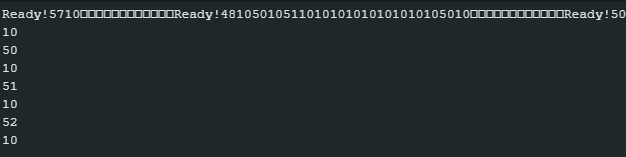
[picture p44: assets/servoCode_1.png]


Okay... I've figured it out. After looking at the Arduino forums and docs, I found that I need to use "serial.parseInt" instead of "serial.read". Basically, "serial.parseInt" reads the whole string of numbers I give it and keeps it in decimal form. "serial.read" on the other hand, only reads the first number and converts it to ASCII.

After testing it, it now outputs the right numbers, but outputs a 0 after everytime I input. After reading a bit more, I found that I need to change the settings from "New Line" to "No Line Ending".

Next, I need to see how I'm gonna select a finger to control. I want to add a prefix to each number. The microcontroller will read the prefix, then the angle. This way, it'll know which finger I'm talking about when telling it an angle.

### Build
I printed out the parts for the thumb in PLA. 

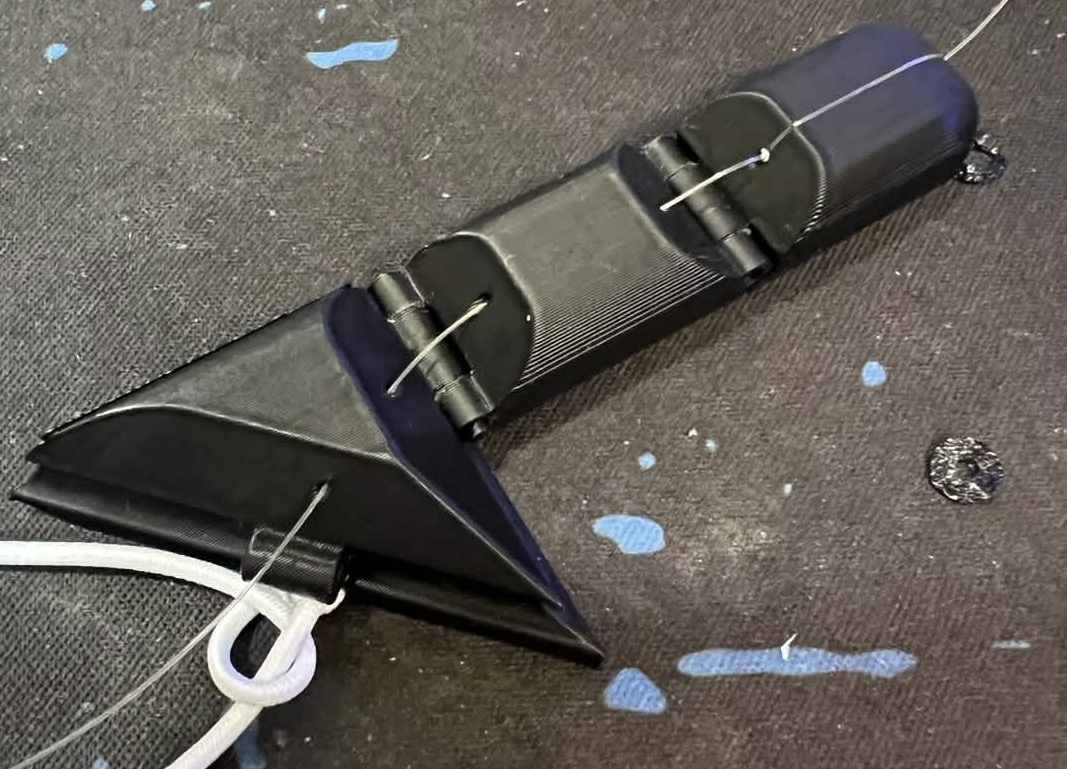
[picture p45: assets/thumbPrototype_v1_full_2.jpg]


After building the thumb, I found that the holes from segments 2 and 3 aren't aligned well, so I decided to take another look at the assembly. 

In the assembly, the fingers weren't lining up either, so it wasn't a 3D printer problem. 

Turns out, I've been using the same cut path/angle for both the elastic cord and the fishing line. This is a problem because the hole for the elastic cord is longer than the hole for the fishing line. Although the path was perfect for the elastic cord, it wasn't for the fishing line. 

To solve this, I created a new path just for the fishing line. Now they line up perfectly in the assembly.

Another problem I faced when building the finger was the tolerances on the pin holes between each finger segment. The pins would just fall straight out. To solve this, I will change the rod diameter from 2mm to 2.2mm.

I also wanted to start building the electrical circuit for testing. Turns out, I was running super low on male to male Dupont wires, so I couldn't color coordinate the wires well. I also accidentally released the magic smoke on one of those breadboard power supplies.

Anyways, here's the final product:

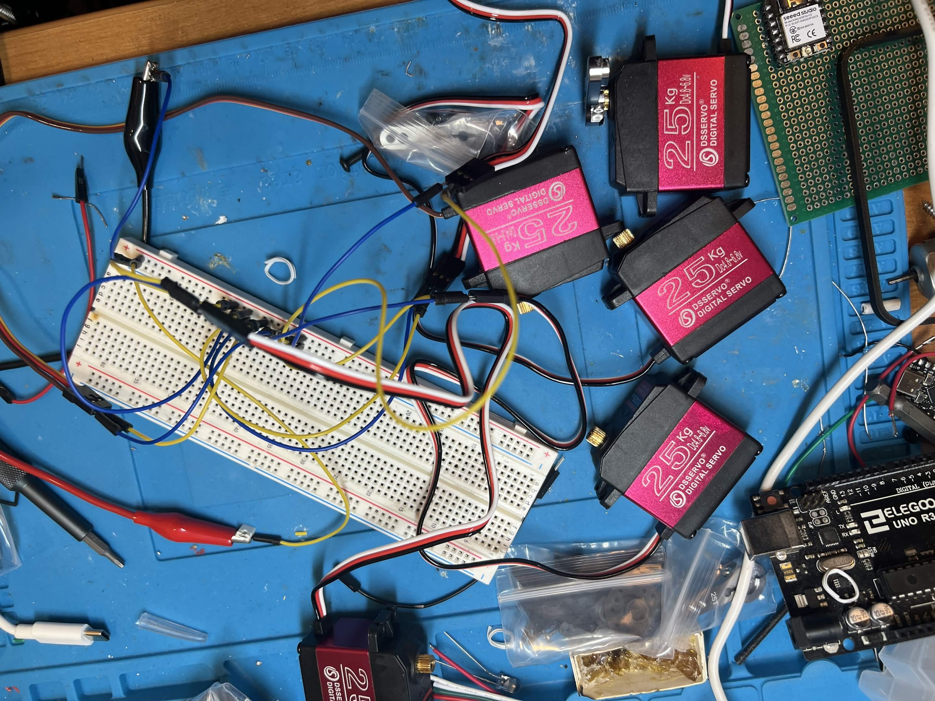
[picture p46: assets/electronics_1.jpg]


Underwhelming? Yeah I swear I'll clean it up one day. The Dupont wires are coming on Friday, so I want to complete the code tomorrow. I'll also print the palm tomorrow. 

## April 2nd, 2026 - Thursday
Hello! Today, I'll finish the servo testing/callibration code.

I finally got it working! It now outputs the finger and the angle that I want. When I input "T90," it outputs "Thumb90". 

Now that it's working, let's move on to controlling actual servos. 

Under each of my elif statements, I've added a "fingerServo.write(servoAngle)" function.



The microcontroller should be able to control the servos now.

## April 3rd, 2026 - Friday
### Design
Hey guys! Today, I want to design the forearm where it will house the servos that control the movement of the fingers. It'll be difficult to cram 5 servos into the forearm, but I'll try my best to make it work. 

Now, I'm thinking of designing the forearm around the servo housing, so I will need to make the servo housing first. 

Since the forearm is wider than it is deep, I'm thinking of positioning the servos horizontally as opposed to vertically. 

This was my first design.


I quickly noticed a problem in this design. Since the top and bottom servo would be in the same level, the string of the bottom servo would knock into the horn of the top servo. 

To negate the issue, I decided to position the servos kinda like this instead.



Here's another design based off of that



I dont really like this design either because it is too wide. I have one more design idea that might work. It involves stacking the servos vertically on it's side instead. 



Although this sketch doesn't show much, I like this design way more since it expands vertically instead of horizontally. The only downside of this design is that the bottom servo has to be on the same height/direction of one of the other servos. This runs into the same problem that I addressed with my first design. I could fix this by making that final servo face forward instead of being on its side. 

I'll fix this problem and start extruding the forearm.



I designed it so each servo can slot into it's designated slot. The each servo will also be screwed into the bar above for more security. I can then drop it right into the the forearm casing. 

I'm thinking of rotating the fifth servo casing 90 degrees. This will align it's horn to the middle of the forearm.

I'm done! 



I added the screw holes and the proper casing for the rotated servo. I made the holes 2.9mm because I didn't have threaded inserts to make the hold stronger. 

Next, I'll print it out and test the tolerances for the print.

I KEEP MAKING THE SAME MISTAKES ON EVERY PRINTTTTTTTTTTT. I forgot to account for the wire stub again so it doesn't fit when the wire stub is facing the flat portion.



The fix is rather simple: just narrow down the main body of the servo holder. It's kind of annoying that I made this mistake but at least it's a fairly easy fix.

Time to send the print to the printer!
### Code
Today, I also wanted to get started on the OpenCV code. I'm a beginner to python and I've never worked with the OpenCV library so it might be a bit difficult for me to program it.

Okay so this is way more complicated than I thought it would be. I think my goal for today will be for OpenCV to open my camera. 

After installing OpenCV, I decided to take a look at some of the example codes on the internet. I learned that you need to declare what camera you plan to use. Since I only have 1 camera, I used the default, "0"

Something cool thats kinda obvious now that I've learned about it is that OpenCV processes each frame individually instead of just looking at the video. I'm not sure if that makes sense or not. 

Anyways, after running my code, the window thats supposed to show what my camera sees just straight up crashed without displaying anything. After looking up my problem, I found out that I need to add a line of code that tells my PC how long the pictures need to be shown for, otherwise it'll overload the computer. 

After the fix, everything showed up fine! Until... I wanted to close the window, but it came back! I had indeed forgot to add a way to escape the "while True" loop.

Once again, Google came to the rescue and told me how to put in a line that would detect whenever the window is closed and terminate the running code.

AFTER ANOTHER GOOGLE SEARCH, I found out that "waitkey(1)" doesn't just wait until 1ms has passed, it outputs the ASCII code of the key that is pressed within that period! So, I just need to add an if statement that checks if that ASCII code is equivalent to, lets just say, the escape key. When I press the escape key, it should stop the program entirely.

And it works!

I still have a bit of time to work on the project today, so I'll get started on the hand tracking.

After some research, I found that there are two ways to do hand tracking, contour detection and landmark detection. contour detection works by detecting colors similar to the target. So it's kinda like a green screen thing. Landmark detection, on the other hand, works by plotting points at specific places on the target. So for your hands, it would plot points on each of your finger joints. I'll probably choose landmark detection because it seems cooler and more accurate. 

For landmark detection, I can use a library or train my own model. Since I'm still a beginner and short on time, I'll choose an existing library. One of these libraries is google's Media Pipeline. On it's website it says that its compatible with python, which is perfect for my project.



Okay, apparently OpenCV outputs in BGR and MediaPipe reads in RGB, so I'll need to convert it. In the while loop, I'll add a function that automatically converts each frame after it is taken. I hope it doesn't add lag to the stream.

Something that I don't like about OpenCV is that it takes a long time to boot up after I run the code. I'm estimating around 1-2 minutes. I'm not sure what to do about it but yeah.

Anyways, I've converted the BGR to RGB so I'm kinda curious what everything will look like. Well, after I started the code, it looks identical so I'm not sure. Then I realized I forgot to change the image it's showing to the RGB feed. 

WOW it looks weird. Everythings more blue now instead of red. Anyways, back to coding.

All of the code that people have used in the past uses a different type of MediaPipe which uses different functions so it looks like I'm on my own.

This project is honestly a lot harder than I thought it'd be but I think I'm on the final stretch.

After running my code, I ran into the problem of "serial.serialutil.SerialException: could not open port 'COM3': PermissionError(13, 'Access is denied.', None, 5)". Another simple fix. I had the serial monitor running on Arduino IDE so it interfered with my python code.

After running into error after error, I decided to just use mediapipe's example code as a base to start off of.

Right off the bat, I was running into less errors. My goal is just to feed the camera stream into mediapipe's hand detection function, and it should just spit out a video that has hand detection. However, like everything, it isn't as simple as it seems. Running into more errors, I realized I need to have the bundle downloaded. After downloading the bundle, I still ran into more errors with the path to the bundle not being right, despite it being right. 

I decided to just go to bed since I was just tired of the errors. Maybe it'll fix its self tomorrow.

## April 4th, 2026 - Saturday
### Design
Last night, while waiting for OpenCV to boot up, I would work on attaching the servos to the servo mount. It's kind of impressive how heavy it is. I'm glad I decided to put it all in the forearm instead of the hand.


Next I need to design a forearm where the hand will mount to. I'm thinking of making the bottom of the hand a little more narrow to look more like a hand. I also might have to change the location of the fishing line holes.

Progress Check!



I'm a little worried that the fishing line will be rubbing against things when being pulled and retracted, so I'll slip a piece of PTFE tubing over the line when I'm building it.



This is going to be what the final product is going to look like. I still have to make some minor adjustments but it should be ready for printing soon



I added holes for the servo mount to screw into the back plate. I also added a big hole for the fishing line to come out of the hand and into the forearm. Lastly, I extruded a triangle support to help with the stress placed on the backplate. The sliced model came out to 73.4g, but I think I can get the model to weigh a bit less. 

Firstly, the big block supporting the last servo has no use since gravity is not pulling in the direction of the block. Removing this will remove a whopping 5g. I could also round out the corders of forearm. This brings the final filament cost to 65.8g. BUT WAIT, THERES MORE!! By reducing the infill percentage to 7%, I bring it down to 62g. 

Wow I saved a total of 10 cents...

Anyways let's print it out.

10% through the print, I realized that I did not add screw holes for attaching the hand to the forearm. I canceled the print and added the holes. I decided to print out the hand first at a smaller layer height to make the circles more circular.

After printing the palm out, I wanted to test out the tunnels for the fishing line, but I could not thread a line through any of the tunnels.

To solve this, I'll expand the holes to 2mm and redoing the paths.

I learned how to use 3D sketching to draw out proper paths for the sweep cuts. 3D sketching is kinda weird since I'm used to just sketching on a plane/face. I had to adjust each point in all 3 axis.



After slicing it it came out to 22g, cheaper than ever! It's probably because I used wider tunnels this time.

Next, I'll have to print out the fingers. For the big pin that connects the fingers to the palm, I'm planning on using filament as the pin. The filament I use has a thickness of 1.75mm. Although the holes of the finger are 2mm, I can use filament because of it's tendency to bend due to being on a spool.

Time for forearm print take 2. Slicer says it'll take 60g, so let's print it. It'll finish around midnight so I'll update you then.

### Code
AHHHH NO MORE CODE PLEASE.

Welcome back to the_idk's coding session where you see a beginner absolutely suffer through coding in python.

Today, I want to debug my code from yesterday and finally have hand tracking.

OMG IT FINALLY WORKS, I JUST MADE A TYPO!!! So a few minutes ago, I gave up and put my code into Claude, and it told me I just made a one word mistake. I'm kinda disappointed but at east it finally detects my hand.



This is so cool. I can't believe it actually works. 

Next, I'll move on to detecting whether each of my fingers are open are closed, then sending that to my microcontroller. I'll do this by comparing the node distance between each finger tip and and its respective MCP. The MCP is the joint that connects the finger to the palm.

## April 5th, 2026 - Sunday
### Build
Today, I want to assemble the whole hand and calibrate all the servos.

First, I need to assemble the hand. I inserted all the pins between each finger segment, binding the fingers together. After repeating that 5 times, I took a spool of filament and threaded it through MCPs. I also put in a pin for the thumb's MCP. 

After that, I threaded and tied all of the fishing line and elastic cord. I made sure it leave a lot of extra fishing line to ensure I'd have enough to tie onto the servo. 

Third, I threaded all the fishing line into the hole in the forearm and bolted down the hand. At first, I used a M3x16mm bolt and it didn't go down all the way. During my attempt of removing the screw, I stripped it's head. I had to use pliers to get the bolt out. I then replaced it with a M3x8mm bolt which fit perfectly.


Then, I bolted down the servo mount onto the forearm. I honestly think that I dont even need to screw it down, but it's better for strength and security.


### Testing
After I was done, I wanted to test each individual servo to see if it was working. I hooked up the top servo to my Arduino and PSU. However, when I said "T90," it spun, but started twitching like crazy. Looking it up, apparently I need to have a common ground between the servo and Arduino. This basically means that I need to bridge the grounds of my PSU and Arduino Uno. This was hard, since I somehow lost my breadboard, which my already sketchy wiring was going to be way worse.

After connecting the grounds, it seemed to work perfectly. I sent "T0," and it turned to 0 degrees. But when I sent "T180," it turned way past 180. Once again, my best friend, Google, comes to the rescue! The function, "servo.write(angle)," only works with 180 degree servos like the SG90. The servo library, however, does have another function, "servo.writeMicroseconds(Microseconds)". I'll have to tune the PWM signal now, not the angle. Which also means I have to rewrite some code. AHHHHHHHHHHHHHHHH

## April 6th, 2026 - Monday
Well, yesterday was the end of my spring break. I was hoping to finish this project but I guess not. 

I worked on the README and BOM of this project.

## April 10th, 2026 - Friday
Hey guys! The breadboards came earlier this week but I didn't come around to wiring up the hand until today. My wiring is kinda messy but it got the job done.



Unfortunately, one of the servos I bought spins in the opposite direction, so I'll have to swap its places with another servo, probably the middle one. It's a bit inconvenient but at least I don't have to buy a new servo.

I calibrated the servos that turn in the right direction. 1845 microseconds seems to be perfect for turning 180 degrees. 

Dang I wish VS Code had a spell check for markdown, I'm probably making so many spelling mistakes in this journal lol. 

WAIT THERE'S AN EXTENSION!!! Okay, so I just installed it and it shocked me how many spelling mistakes there are in my journal. I'm glad I downloaded it.

That's it for tonight, I'll hopefully finish calibrating the servos tomorrow.

## April 11th, 2026 - Saturday
Hey guys! Today I started by swapping the counter clockwise servo with the middle finger servo. 

Next, I want to make some adjustments to the python script. Since I changed the servo.write to servo.writemicroseconds, I need to swap out the 180 for 1845. 

Now, I want to test if the servos actually spin when I start the program.

Ther servos did not even move. After an hour of debugging, I finally found out that I need to use Serial.parseInt(SKIP_NONE). I think the parseInt was timing out so it didn't read all of the digits I was sending it. 

Now, I just need to tie down all the fishing line to the servo horns. 

You know what's funny about hardware? Everytime you think you're close to finishing your project, there's another problem that shows up out of nowhere. While I was trying to tie down the string to the servo, I found it very hard to tension the wire. Additionally, the wire is kind of stretchy, that didn't help with the tension either. A few weeks ago, I made a spool that attaches to the servo horn, but that design isn't good so I'll redesign it. For this new design, I want to take inspiration from [Made by Horizon](https://www.youtube.com/watch?v=aHFo-7ZK1Bk&t=697s), who made a really good spool roller for his hand. His spool design fits better onto the servo horns because it sits on top of it instead of in it, like mine does. His two sided design also makes it easier to print and construct.



As opposed to Made by Horizon's project, I used one hole because I am not running a dual string system like he is. 

I'll be printing this prototype on my newly fixed Ender 3 because I'm printing something on my P1S right now. 

I also realized that I'll need to update the dimensions of the forearm so that it can freely rotate. The current backplate of the forearm doesn't let the horn rotate 360 degrees. Instead, it just blocks it from moving.

Actually... I think I'll just see if I can get away with not redesigning the forearm backplate.

After the the I printed out one of the spools, I noticed that it was way too thin. To fix this, I extruded the inner circle 3mm and the outer circle to 2mm.

Unfortunately, the old spools were so thin that they were cemented to the glass bed. It took some time, but I eventually got the spools off with my fingers. I then started the print using black PLA. Almost instantly, the print failed. I cleared the print bed and tried again... and again... and again. I had to reset it so many times that my P1S was done printing. I ended up just printing it on my P1S and it came out perfectly.

While attaching it to the servo, I found it very hard to thread the fishing line through the small hole. I also feel like the circumference was too small so the fishing line didn't really get pulled enough.

I designed a new one with a bigger thread hole and a larger circumference. However, this means I can't get away without making a new forearm back plate. Before designing a new backplate though, I want to test if this new spool is better.

While testing, I noticed that OpenCV would freeze up when I put my hand in front of my camera. It doesn't completely freeze up, but it works very slowly. To solve this, I decided to do some research. The first fix was to lower the camera resolution. 4k webcams, like mine, don't improve the accuracy of MediaPipe much, so it's just a performance sacrifice. I lowered by resolution to 480p, hoping for a fix. I also put in the "cv2.CAP_DSHOW" so that the program would boot up faster.

I did fix the slow boot up problem, but the lag was still there.

AHA! I found the fix! First, I fixed the code to only send updates to the Arduino if the my hand changed from open to close, or from closed to open. Also, I removed the delay I placed in the Arduino code that I forgot about. Finally, I changed the camera from 2fps to 4fps. 

Actually? I want to change it to 60fps. I don't think I'll have lag problems anymore. 



Next, I need to move on to my most dreaded task... Redesigning the forearm. I'll make a list of improvements I need to make below:

1. Make it wider, 10mm?
    - This is a maybe fix. I want to make the complete assembly first to see if I really need it.
2. Move hand to the front
    - The line is rubbing against sharp corners. 
    - It's also very hard to thread the fishing line if one is broken/needs to be replaced
3. Make the forearm deeper.
    - I'm not sure by how much yet. I haven't calculated it yet.

I just realized I have to reprint the whole forearm. Reminder to everyone making a project and myself. **ALWAYS** make a full assembly of your project before printing the parts out. You will make a mistake that you'll only find out near the end of your project. 

I can tell that I'm almost done with this project. But everytime I feel like that there's always another bug/design issue that I missed. 

Back to making the assembly. I made this servo model.



Wait it's past midnight so I'll start another journal entry and push this to Github.

## April 12th, 2026 - Sunday
While testing my servos, I found that the monofilament fishing line I was using was deforming after stretching. This caused my robot to lose a ton of tension and not work anymore. Doing some research, I found that other people doing my project used braided fishing line instead. It's roughly the same cost, stronger, and not stretchy at all. 

Looking for the cheapest option, I went with [this](https://a.co/d/0gZXuDRI). It has 100lbs tensile strength, perfect for this project. 

Anyways, it's getting late, so I'll continue this in the morning. 

Good morning guys! Today, I want to finish the new assembly and print out the new parts I'll need. 

I started by finishing the assembly of the servo. 


As you can see, I've modeled the original horn onto it. 

Next, I must redesign the servo mounts. 

I made each mount taller by around 18mm so that the horns can spin freely. 



I also added the little wire stub that every servo has because I keep forgetting to account for that in my 3d prints.

Anyways, I just need to add the mount for the fifth servo and the screw holes and then I can remodel the back plate. 



As you can see, I also made the legs a bit thinner to save on filament and time. Now I need to model the back plate. 

Here's the full new assembly of the arm!



I don't like how there's so much behind it but I'm not sure how I would correct it. Other than that, I addressed all of my fixes. Moving the hand ensures that the every fishing line can reach each spool successfully. In my old design, the fishing line would run and rub into something. This adds friction and wears down the line. 

Anyways, I'm gonna print it and reconstruct the hand once the fishing line comes. 

## April 14th, 2026 - Tuesday
The fishing line arrived today! Right off the bat, I could tell that it was a lot stronger than the monofilament line I was using before. It also had no elasticity at all! When I was trying to cut it, it took a lot more effort. All in all, I think buying the new fishing line was a good choice. 



I disassembled the forearm and tried to restring the fishing line, but the new fishing line is double the thickness of the monofilament one. I think I'll have to expand the holes to 2mm instead of 1mm.

I only printed one finger of the new fingers so that I don't waste filament in case the holes are still too small. Thankfully, the holes were at the perfect size. The new finger feels a lot sturdier with the new fishing line as well. I dont know why.



## April 15th, 2026 - Wednesday
Hey guys! Unfortunately, I was not able to work on the hand that much today because I came home really late today.

However, I did finish the finger redesigns by resizing the fishing line hole in the thumb segment. It was pretty easy since the paths were already planned out.

I sliced it in the slicer and used Bambu's Support for PLA as a support interface. I always either use Support for PLA or PETG as a support interface because it creates a smooth surface for the hinge mechanism.



As I'm writing this, I forgot to plug in the PTFE tube from the AMS to the main feeding tube for the extruder.  Gladly, I caught it early before it unspooled all the filament. 

Anyways, that's it for today! Waiting for the prints will take a while.

## April 16th, 2026
What's up guys! Today, I worked on reconstructing the hand. 

I first started by removing all of the support from the newly printed fingers. They basically fell of because of the support interface so it was really easy.

I then finished disassembling the old fingers so that I could reuse the old pins. I didn't want to reprint all the pins and waste filament. After I was done with that, I connected all the segments together. 



I strung up all the elastic cord and then it was done! 

Next, I needed to finish reconstructing the forearm. I screwed in the servos into the new mount but my electric drill's battery was dying so I took a break to eat dinner while it charged.

After dinner, I finished screwing everything in and it looked really chunky. I'll fix this in future iterations.

Since the overall construction of the arm was done, I moved on to trying out the new fishing line. I had a bit of trouble tying the fishing line because it wouldn't stay tensioned. I eventually gave up and just decided to turn on the servo without fully tensioning it. To my surprise, it worked really well! The finger was able to pull all the way down.



Well that's it for today!

## April 17th, 2026 - Friday
It's finally the weekend! I can't wait to finish up this project. 

Now, something I didn't address yesterday was the flex of the back plate. When the string is pulled by the servos, the back plate tends to flex forward. On the old version, it didn't face this problem because it was not only smaller, but had a bit of support on the side. So to stop the flexing on the new design, I will model and print out supports for the top.

I just ended up extruding a long rectangular prism. I decided on a simple design because I dind't want to overcomplicate my current project too much. Here's the updated assembly!

 

Like always, I'll print it in black PLA. 

I printed it out, but one of the sticks had a bit of problems with it's first layers. Additionally, everytime it would just fall out of the forearm everytime I try to fit it in. 

So, I redesigned it. I decided to use the existing screw holes from the hand. Now, it will mount securely onto the forearm, preventing any slippage. 





Earlier, I noticed that the string was losing tension, probably from my bad knots, so while I waited for the new support to print, I tried to untie it. However, I eventually gave up because it was taking too long and just cut it instead. Later, I plan to retie it tighter. 

## April 18th, 2026 - Saturday
Today I want to mount the support piece and redesign the spools. 

Installing the support was pretty easy.

I want to redesign the spool a little bit because the string was hard to attach when it was connected to the horn. The horn gets in the way of my fingers so I have to awkwardly push it in. 

For my first prototype, I made the side thinner again and a bit bigger. I can now use a 4mm hole instead of a 2mm, making it easier to push the string in. I also placed the hole for the string behind the horn instead of in front of it so it's now easier to push it in. 



I sliced it at 100% infill because of how thin it is.

I screwed in the new horn once it was finished and it was really easy to tie down the fishing line. I started by setting every servo to 0 degrees. Then I screw down the new horn with the fishing line facing in the directions of the fingers. I make a loop around the spool so that the fishing line has a path to go through. Finally I tie the fishing line down.



When testing, the hand worked perfectly with no problems! I'm finally so close to finishing! I'm so happy!

Next, I need to print out the rest of the spools so I can finish the rest of the hands

Sooooo I completely forgot that I need to calibrate each servo to a certain angle. The thumb servo went to it's max and broke my servo mount. So I'll have to reprint my servo mount. 



I hope this doesnt mean I have to retie all the fishing line...

After the new mount finishes printing, I will calibrate all the servos.

Ayyy it's done printing!

I mounted all the servos to the servo mount and then I started calibrating. So far, each of the servos have had wildly different numbers. I only got three of the servos calibrated today: thumb, index, and middle. Since it's getting late, I'll probably calibrate the rest tomorrow. 

## April 19th, 2026 - Sunday
Hey guys! Today I wanted to redesign the forearm mount because of the lack of support. Even with the new support I added yesterday, it was still bending.

Like always, I want to model my parts so they use the least amount of support as possible. 

After thinking about it, I realized that I don't have to fully redesign the forearm back plate. I just need to add some parts to the support and cut more screw holes for the hand. 

First, I redesigned the support to screw in on both the top and bottom of the forearm. On the bottom, I will use two SHCS so that the bottom is flush with the table. On te top, I'll still stick with BHCS. 

I also extruded triangles on the top and bottom of the support to distribute the force of the servos. 


Lastly, I extruded a block on top of where the servo mount will sit. Since the servo mount pulls its self up when pulling down the servo, the block will hopefully absorb some of the force. 

Here's the full new design!



Once the new parts finish printing, I'll put together the new, hopefully more strong arm!

Alright, it's done printing now and I put it all together. I forgot to mention this but I'm in the process of moving setups so all of my materials are split between two rooms. I have to run to and from that room when I'm missing a part. 

Somehow, one of the servos started spinning in one direction constantly, which I didn't even know was possible for a servo to do. I decided to just turn off the power supply. When I turned back on the power supply, it worked perfectly so I'm not sure what was wrong.

I also had a problem with the fingers getting stuck. It was probably a friction problem, but I don't have or know any lubricants that don't melt PLA. I just used a little water and it seemed to work. After the lubrication, none of the finger seemed to get stuck. 

Finally... the last part of the project... clicking run on the code...

AND IT WORKS!!!

FINALLY! AFTER 2 MONTHS OF WORK, ITS DONE!



Well, I think that's enough for today, I'll start preparing for submission tomorrow. 

## April 20th, 2026 - Monday
Since it's done, let's start prepping this for submission to fallout. 

Okay so apparently my project can't just be a big fire hazard so I'll clean it up.

To eliminate the breadboard, I'll solder all of the power cables together. I'll cut off one end of the dupont wire and solder the bare wire together. 

My soldered together wires looked kind of bad but they worked. 


I hooked everything back up and it looked way cleaner without the breadboard, I might also use some zip ties later to clean everything up. 



I felt kind of tired of working on the hardware so I just worked on organizing the repository for the rest of the day. 

## April 21st, 2026 - Tuesday
Happy tuesday! 

Today, I started by moving more files from my separate folder into the repository. I also added a bit more to the README. 

I opened up my assembly final to take another look at it, but turns out it broke somehow, so I had to re mate some parts. I also made it so the servo horn and spools actually line up in the assembly so I can properly define them. 

After I was done with the assembly, I wanted to render the 3D model in Blender, but after watching a few videos, I thought that it was way too complicated and decided to try and render it in SolidWorks. I added colored the support and servo mount white to act as a accent color. I also added a directional light which made it even better. Lastly, I added a scene and removed the cartoon lines from the edges of the parts. At first, I was admiring it, but then I noticed the jagged lines on the edge of the parts. I thought anti-aliasing was supposed to fix it, but I guess not.



Trying to fix this, I looked it up. Apparently I was supposed to use SolidWorks Visualize, which is SolidWork's rendering software, but it kept crashing. Doing some more research, I found that I probably needed to update my GPU drivers, but after I did, it still didn't work. 

Since It was getting late and I had some homework to do, I didn't dwell on it too much and decided to log off for the night. 

## April 22nd, 2026 - Wednesday
I didn't do much today, but I did work on the README! It looks a lot better since I took inspiration from notaroomba. 

I centered some of the titles and added the story of this project.



## April 23rd, 2026 - Thursday
Hey guys! Today, I want to finish organizing all the 3D models into the right places and just make progress to submission in general. 

I started off by adding and changing some things on the BOM. I added the all the materials that were missing before: PETG, elastic cord, and fishing line. I also added the correct values for the filament usage. I separated the parts based on different settings. For example, the finger segments use support interface and the spools use 100% infill. The support, palm, and back forearm plate is printed with default settings.



Then I remodeled the palm because I had lost the original file somehow. It wasn't that hard since I only had to redraw the fishing line routes. 

After that, I checked to see if I was missing any STEP files, but turns out I was missing the thumb model. I went into CAD to save it as a STEP files, but turns out it was missing the holes for the fishing line and the elastic cord. It took a bit, but I finally remembered how I cut the holes into it. 



That's basically all I did today. Hopefully I can submit this weekend. 

## April 24th, 2026 - Friday
Happy Friday! It's finally the weekend, hopefully, I'll be able to ship. 

I started off by updating the wiring schematic to remove the breadboard. 



I then removed the filament from the BOM and started working on the list of 3D printed parts. It took a while, but I individually sliced each part to see how much filament it used, and put it into a spreadsheet. I then exported it as a CSV. To import it into markdown, I used this tool: https://convertcsv.com/csv-to-markdown.htm 



After reviewing the submission checklist, it seems that I have everything needed except the zine. I dont have much experience in graphic design, so this might be a bit hard. First, I want to choose a color pallette. I might go with black, red and white since that's the main colors on the robot. 

Unfortunately, the zine template Hack Club gave me doesn't seem to fit on A5 paper like specified, so I'll start it tomorrow. 

## April 25th, 2026 - Saturday
Hey guys! I just got confirmation that it's supposed to fit like that on A5 paper, so I will try to finish the project today! 

Here are the zine requirements:
- [x] Be A5 Dimension
- [ ] Be in my README
- [ ] Describes what it is
- [ ] Have a central graphic
- [x] Have a QR code to my GitHub repository
- [x] Have my name, age, and state/country I'm from

I'm so done with this project. One of the motors started tweaking again and destroyed the servo mount. This project is starting to get on my nerves. I don't even know why it randomly started spinning in circles. 

Welp, I guess I'll just have to rebuild hand again. After it finished printing, I tried to put it back together as soon as possible because I only had an hour until it needed to be presented at a show and tell. I eventually finished it, one minute before the show and tell started. The show and tell went okay.

Next, I need to finish up the zine. I'll be checking stuff off as I go. Since it's already in A5, I'm already 17% done! Once again, I'm following this color pallete:


I only got 3 of the check marks done today. I still need a description and the main picture, but I can't take the picture since its getting late. 



While I wait, I wanted to experiment with print in place hinges. From what I've heard, they require any need for support. 

To get started, I modeled the 3 segments all in the same part. It took a while to define everything because I kept over defining it. Eventually, I got to a design that looks like this. I essentially copied over the v4 finger. 


I then modeled it so segments 1 and 3 had a cone coming out of it to act as the pin. So now the finger looks like this. Everything has a clearance of 0.2mm right now and I'll adjust it based on how well it prints.



I sliced it Bambu Slicer and it came out to around 8g of filament



## April 26thm 2026 - Sunday
The finger turned out decent. It wasn't a smooth as I would've liked so I'll stick to the v4 for now. Anyways, it's like 2 in the morning so I will go to sleep and keep working tomorrow.

Good morning guys! Continuing on with yesterday, I want to finish the zine today and submit! Here's the checklist from yesterday:

- [x] Be A5 Dimension
- [x] Be in my README
- [x] Describes what it is
- [x] Have a central graphic
- [x] Have a QR code to my GitHub repository
- [x] Have my name, age, and state/country I'm 

Earlier, my sister helped me take some pictures.



I'll remove the background in Canva. 

I'm finally done! I added the red stripe to make it pop out more. 


Now, I have to find a way to make the demo video. Wait actually, I have a great idea. 

https://www.youtube.com/watch?v=Rfja3hf1nRA

I've taken the video, now I want to double check everything so I know I'm not missing anything. 

I think I got everything, so I'll submit now.

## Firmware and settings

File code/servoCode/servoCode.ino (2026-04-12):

// Libraries
#include <Servo.h>

Servo thumbServo;
Servo indexServo;
Servo middleServo;
Servo ringServo;
Servo pinkyServo;

// Variables
char finger = 'T';
int servoAngle = 0;

void setup() {
// Pin Assignments
thumbServo.attach(3);
indexServo.attach(5);
middleServo.attach(6);
ringServo.attach(9);
pinkyServo.attach(10);

// Serial Monitor
Serial.begin(9600);
Serial.setTimeout(10);
Serial.print("Ready!");
}

void loop() {
  if (Serial.available() > 0) {
    char finger = Serial.read();
    servoAngle = Serial.parseInt(SKIP_NONE);
    
    if (finger == 'T') {
      Serial.print("Thumb");
      thumbServo.writeMicroseconds(servoAngle);
    }
      else if (finger == 'I') {
        Serial.print("Index"); 
        indexServo.writeMicroseconds(servoAngle);
      }
      else if (finger == 'M') {
        Serial.print("Middle");
        middleServo.writeMicroseconds(servoAngle);
      }
      else if (finger == 'R') {
        Serial.print("Ring");
        ringServo.writeMicroseconds(servoAngle);
      }
      else if (finger == 'P') {
        Serial.print("Pinky");
        pinkyServo.writeMicroseconds(servoAngle);
      }
    Serial.println(servoAngle);
    }
  
    
  
}

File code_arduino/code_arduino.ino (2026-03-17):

// Libraries
#include <Servo.h>

// Servo Names
Servo thumbServo;
Servo indexServo;
Servo middleServo;
Servo ringServo;
Servo pinkyServo;

void setup() {
// Pin Assignments
thumbServo.attach(5);
thumbServo.attach(11);
thumbServo.attach(12);
thumbServo.attach(15);
thumbServo.attach(16);
}

// Serial Monitor
Serial.begin(9600);
Serial.println("Ready!");

void loop() {

}

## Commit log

2026-04-01 code and repo organization
    [Finger1.SLDPRT, Finger2.SLDPRT, Finger3.SLDPRT]
2026-04-06 April 5th Project Update
    [BOM.csv]
2026-04-11 4/10/26 Project update
    fixed spelling of journal, began calibrating servos.
    [servoCode.ino]
2026-04-12 APRIL 12TH PROJECT UPDATE
    [DS3225MG.SLDPRT]
2026-04-15 journal update
    [BOM.csv, DS3225MG.SLDPRT]
2026-04-24 repository organization
    [Assembly.SLDASM, BOM.csv, DS3225MG.SLDPRT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]
2026-04-25 april 25th 2026
    [BOM.csv, BackStand.STEP, List Of 3D Printed Parts.csv]
2026-04-26 almost done!
    [Finger2.SLDPRT, servomount.STEP]
2026-04-26 im finally done!
    [BOM.csv]
